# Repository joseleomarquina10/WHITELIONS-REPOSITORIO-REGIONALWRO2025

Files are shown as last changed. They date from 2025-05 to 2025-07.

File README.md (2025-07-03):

# **TABLA DE CONTENIDOS** 

- [**NUESTRO RECORRIDO**](https://github.com/joseleomarquina10/WHITELIONS-REPOSITORIO-REGIONALWRO2025/tree/main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)
- [**IDEAS Y PRINCIPIOS**](https://github.com/joseleomarquina10/WHITELIONS-REPOSITORIO-REGIONALWRO2025/tree/main/OTRO#ideas-y-principios)
- [**DOCUMENTACIÓN DEL HARDWARE**](https://github.com/joseleomarquina10/WHITELIONS-REPOSITORIO-REGIONALWRO2025/tree/main/ESQUEMAS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)
- [**DOCUMENTACIÓN DEL SOFTWARE Y DEL CÓDIGO ARDUINO**](https://github.com/joseleomarquina10/WHITELIONS-REPOSITORIO-REGIONALWRO2025/tree/main/SRC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)
- [**FOTOS DEL EQUIPO**](https://github.com/joseleomarquina10/WHITELIONS-REPOSITORIO-REGIONALWRO2025/tree/main/FOTOS-EQUIPO)
- [**FOTOS DEL VEHÍCULO**](https://github.com/joseleomarquina10/WHITELIONS-REPOSITORIO-REGIONALWRO2025/tree/main/FOTOS-VEH%C3%8DCULO)
- [**VIDEOS** ](https://github.com/joseleomarquina10/WHITELIONS-REPOSITORIO-REGIONALWRO2025/tree/main/VIDEO)

# **NUESTRO RECORRIDO**

Mediante este repositorio les mostraremos detalladamente el proceso y recorrido del proyecto WHITELIONS, con esto buscamos explicar paso por paso y ordenadamente la construcción de nuestro carro llamado WHITELION, así como también destacar su evolución y nuestro aprendizaje de cada falla, pues para nosotros fallar no es fracaso sino una oportunidad para acercarnos más al éxito.

## **EQUIPO** 

Nuestro equipo consiste de dos miembros y un coach, somos WHITELIONS de Yaracuy. Este es nuestro tercer año participando juntos en WRO, pero esta es nuestra primera edición en la categoría Fututos Ingenieros.  A continuación, se les presenta los integrantes del equipo:

    MIEMBROS:

-	Guillermo Herrera del Colegio El Ángel 
    - guillermoaherrerab@gmail.com

-	José Leonardo Marquina del Colegio Los Ángeles
    - Joseleonardomarq10@gmail.com

    COACH:

-	Luis Barrios
    - luisgbarriosm@gmail.com

Les presentamos los links a nuestras redes:

- Youtube: https://www.youtube.com/@WhiteLions-r5q
    Aquí pueden encontrar videos del desenvolvimiento del vehículo.

- Instagram: https://www.instagram.com/whitelions.wro?igsh=MWYzM2lkdWxreDZrdw==
    Aquí pueden encontrar novedades de nosotros.

## **PRIMEROS PROTOTIPOS Y EVOLUCIÓN DEL DISEÑO**

- ### **Primer Prototipo**
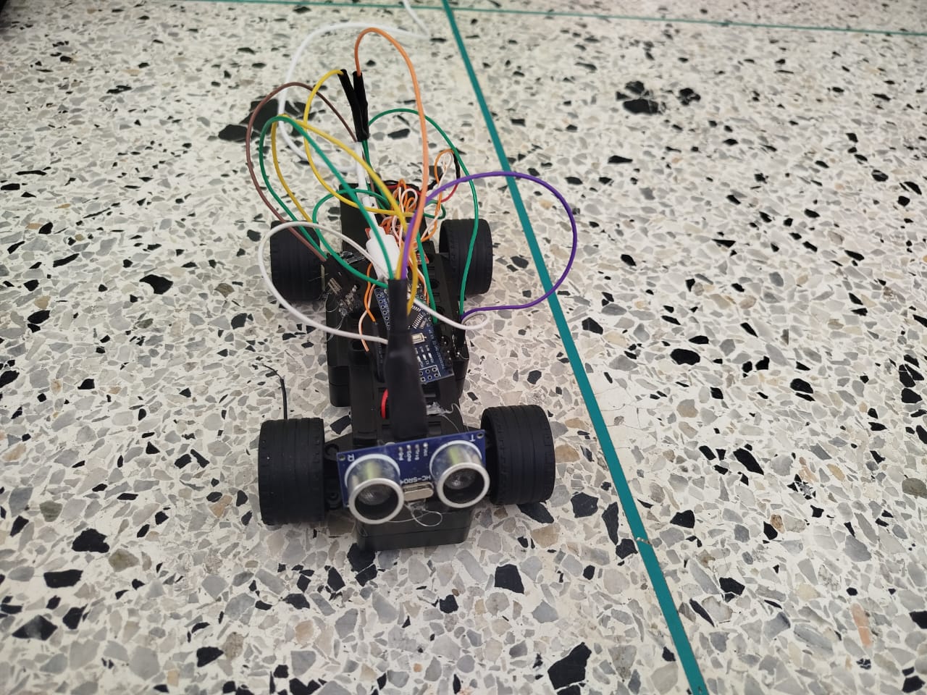
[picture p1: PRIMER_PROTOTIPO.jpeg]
PRIMER PROTOTIPO


Originalmente, utlizamos un kit de carro de lego al cual le instalamos una tarjeta arduino nano y un sensor de ultrasonido, aprovechamos el sistema de dirección y tracción que contaba el carro. Por una parte la tracción funcionaba con un motor dc y por la otra parte la dirección también contaba con un motor dc pero controlaba su radio de giro con una pieza de abanico que limitaba el giro. Además el carro tenía un driver de motor para controlar estos.

Todo este mecanismo lo conectamos con la tarjeta Arduino y aquí nació el primer prototipo del WHITELION, el cual únicamente giraba a la izquierda al detectar una pared al frente y gracias al mecanismo de engranajes de la tracción iba a alta velocidad.

Este primer prototipo nos sirvió para realizar una gran cantidad de pruebas así como también para darnos cuenta de muchas cosas que debíamos mejorar. Rápidamente nos dimos cuenta de que la dirección presentaba muchos fallos pues era controlada por un motor dc, además el chasis del carro era demasido pequeño y estrecho, lo que iba a dificultar ubicar el resto de componentes necesarios. 

- ### **Primer Modelo en Tinkercad**
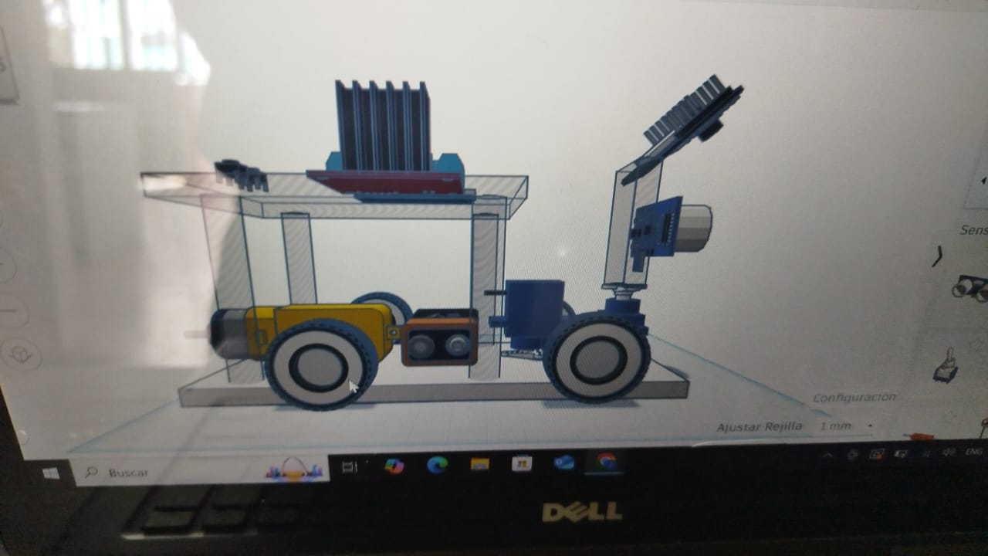
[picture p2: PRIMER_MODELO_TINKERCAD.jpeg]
PRIMER_MODELO_TINTERCAD


Por lo anterior, realizamos un rediseño para imprimir en 3D todo el chasis y la dirección, sin embargo nos quedamos con las ruedas delanteras y su mecanismo de giro, además la nueva dirección sería controlada por un servomotor para más precisión al girar.

Nuestro principio es que el carro sea pequeño por eso definimos el nuevo chasis de dimensiones de 10x15 cm, pero igualmente nos dimos cuenta del poco espacio, por ello decidimos hacerle un segundo chasis al carro y de esta forma habrían dos: Chasis superior, con los controladores y la batería; y chasis inferior, con la traccion, dirección y el sensorores. 

Del carro anterior, también definimos que el ultrasonido funcione como un radar y que se mueva constantemente por un servomotor para detectar su entorno y de alli decidir a donde girar, por ello pensamos en utilizar una torre arriba del servo para colocar el ultrasonido y una posible cámara, además utilizamos un solo motor dc para la tracción para no complicar la programación y porque al probar con dos constantemente se soltaban del eje.

Incorporamos el driver de motor dc L298N para poder controlar la velocidad a través del pwm y por sus conexiones atornilladas, para asegurar una conexión firme. por la misma razón incluimos una base expansora de arduino nano para atornillar.

- ### **Primer Carro Funcional**
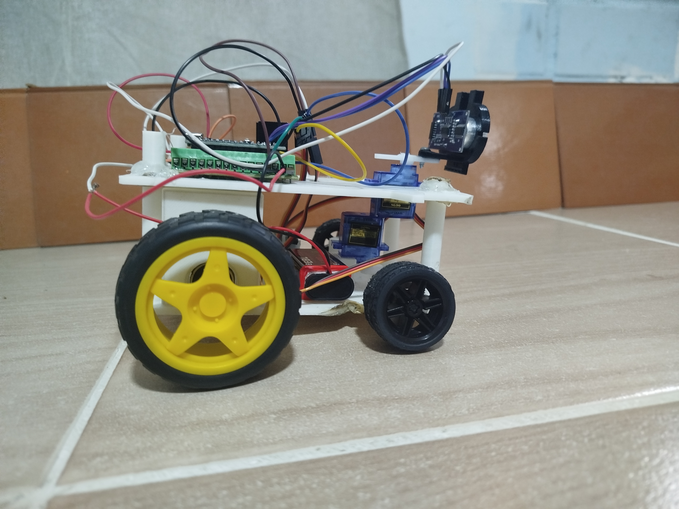
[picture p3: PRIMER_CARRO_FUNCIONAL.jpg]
PRIMER_CARRO_FUNCIONAL


Tras este rediseño notamos que aún era necesario más espacio por ello expandimos el chasis superior a las mismas dimensiones del inferior. 

Notamos que existía un espacio aprovechable en el chasis infeior por el uso de un solo motor así que allí ubicamos la batería y para que todos los cables pasaran de buena forma de chasis a chasis, hicimos una abertura en el superior.

Tras esta expasión del chasis superior ya no podíamos instalar el radar en el chasis inferior, por lo que decidimos hacerlo arriba y con impresión 3D llegamos a este nuevo prototipo, el cual usaríamos en nuestra primera regional.

### **DISEÑO ACTUAL**
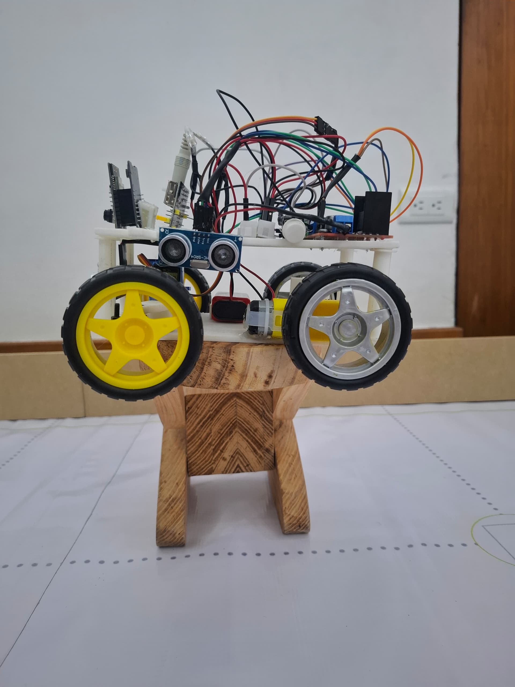
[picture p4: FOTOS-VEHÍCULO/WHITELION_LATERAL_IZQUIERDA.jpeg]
DISEÑO_ACTUAL


Tras nuestra primera regional decidimos descartar el radar pues presentaba muchos fallos, en su lugar agregamos tres sensores de ultrasonido (Uno apuntando hacia el frente y los otros hacia los laterales, uno a la derecha y otro a la izquierda) de tal forma de que el carro detecte cuando haya un vacío y girar hacia allá. Además cambiamos las ruedas de lego por otras de motor DC e incorporamos la cámara ESP32 CAM para la vuelta de obstáculos, sin embargo notamos rápidamente que coincide en posición con el ultrasonido central, por ello dejamos el ultrasonido en el chasis inferior y la cámara en el superior.

También incorporamos una fuente de alimentación para distribuir el voltaje entre la arduino, el driver y la cámara; adicional a esto añadimos dos líneas negativas y positivas de protoboard para complementar.

Debido a los nuevos componentes agregados tuvimos que expandir ambos chasis a dimensiones de 17,5x15 cm, además de reforzar el grosor de la barra de dirección para hacerla más resistente.

Y así llegamos a nuestro diseño actual.

# **CONCLUSIÓN**

Este proyecto fue realmente difícil de desarrollar, pero nos dió mucho aprendizaje dentro del mundo de la robotica y nos brindó experiencias innolvidables, enseñandonos a como manejar los problemas de la mejor manera posible, ya sea en programación del proyecto o en el armado cuando nada queria funcionar y cuando nada se ajustaba a lo que buscabamos hacer, y que aún asi poder salir adelante y hacer un proyecto funcional de competencia, motivandonos a seguir participando en estas competencias.

# **AGRADECIMIENTOS**

Primeramente nos sentimos agradecidos con Dios, con nuestro tutor Luis Barrios y con nuestros padres, por apoyarnos siempre y formar parte de todo este recorrido en futuros ingenieros. Agradecemos de la misma forma a nuestra casa de las olimpiadas MATICES, por darnos sus espacios para poder armar y desarrollar el carro, a nuestros profesores Johan Goyo y Rafael Linarez por orientarnos y a nuestros colegios "El Ángel" y "Los Ángeles".

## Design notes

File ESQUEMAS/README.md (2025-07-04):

# **ESQUEMAS**

## **DOCUMENTACIÓN DEL HARDWARE**

### **LISTA DE COMPONENTES**
 
Instalamos una gran cantidad de sensores y componentes al vehículo. A continuación les presentamos una lista con cada uno de estos:

- Tarjeta Arduino Nano Ch340              x1
- Base Expansora para Arduino Nano        x1
- ESP32 cam Arduino                       x1
- Motor DC Caja Reductora 200 rpm         x1
- Ruedas de Motor DC (Tracción)           x2
- Ruedas de Motor DC (Dirección)          x2
- Micro ServoMotor Sg90 90g               x1
- Sensor Ultrasonido Hc-sr04              x3
- Driver de Motor DC L298N                x1
- Batería 9v y 5400 mAh                   x1
- Rolinera                                x1
- Barra Metálica (tracción)               x1
- cilindro hueco de plástico              x1
- Fuente de Alimentación Mb102            x1
- Pulsador                                X1
- Interruptor                             x1
- Línea positiva y negativa de protoboard x2 

### **ENSAMBLADO**

El carro se divide en dos bases: La base inferior y la base superior. Cada base lleva por dimensiones 17,5x14cm (se incluyen las alas para las ruedas de dirección).

En la siguente tabla se explica en que base se encuentra cada componente Y cada Material:

| BASE INFERIOR | BASE SUPERIOR |
|---|---|
|Chasis Inferior |Chasis Superior |
|Motor DC |Arduino Nano |
|Micro ServoMotor  |Base expansora para arduino nano |
|Rolinera |Driver de motor L298N | 
|Barra Metálica |2 línea positiva y negativa de protoboard |
|Cilindro Hueco |Botón de encendido |
|4 Ruedas motor DC |Fuente de alimentación (con interruptor incluido) |
|Batería 9v |2 sensores ultrasonido |
|Soporte Tracción  |Cámara ESP32 CAM |
|Soporte Dirección | |
|Barra Dirección | | 
|4 Soporte Cilindro| | 
|Sensor ultrasonido| | 
|Soporte Servo | |
|2 Soporte Batería | |  

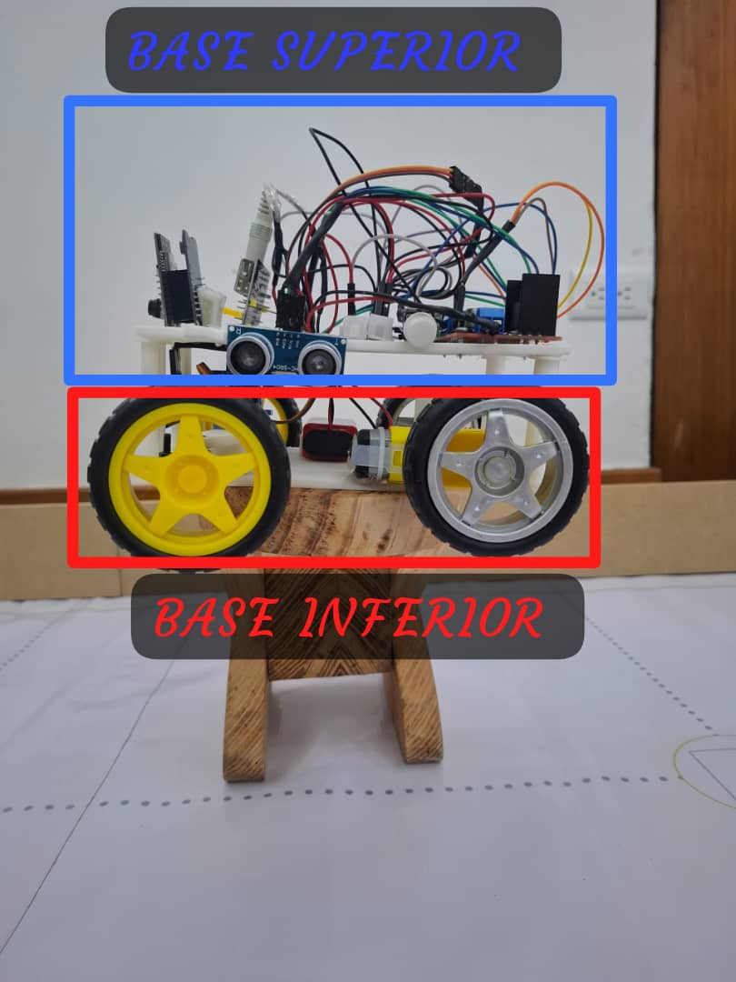
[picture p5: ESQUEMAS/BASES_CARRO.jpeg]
BASES_CARRO


### **BASE INFERIOR**

Esta es la base de tracción, dirección y donde se ubica la batería, además del ultrasonido central.

 Para la dirección Diseñamos un soporte en forma de bloque para ubicar el servo boca abajo, una barra para unir las dos ruedas delanteras y dos soportes en forma de triángulo (similar a las alas para colocar las ruedas) para sostenerlas y mantenerlas en un eje vertical. De esta forma ubicamos las ruedas a una distancia entre sus ejes verticales de 12 cm (Cada eje vertical dista 1cm del chasis de tal forma que las ruedas tengan el mayor radio de giro). Los ejes verticales de las ruedas y del servo deben estar alineados para moverse en paralelo. Ubicamos estos ejes a una distancia de 3,25 cm del borde frontal del chasis, y así dejar espacio para la barra de dirección, esta mide 13 cm (cubre la distancia entre eje a eje de cada rueda y un poco más). El eje del servo se encuentra a 6 cm de cada eje vertical de las ruedas delanteras. La distancia total de punta a punta de las ruedas de dirección es 19,5 cm.

 Para la tracción ubicamos el motor DC tal que su eje horizontal se encuentre a 3cm del borde posterior del chasis, una rueda la unimos directamente al motor mientras que la otra la conectamos por un eje compuesto por una barra metálica y esta se conecta al motor DC siendo envuelta por un cilindro hueco de lapicero y una pieza de lego negra, la barra se fija al cilindro con silicón para que no quede inestable al girar, además la barra también se fija a una rolinera de diámetro 2cm para asegurar que ambas ruedas estén a una misma altura. Luego se fija el soporte en forma de U en la rolinera para dejarla fija. Las ruedas traseras se encuentran a una distancia, cada una, de 1,5 cm del chasis y la distancia total de punta a punta de ambas ruedas de tracción es 18 cm.

 Note que en la parte central del chasis inferior aún queda un gran espacio aprovechale, allí ubicamos dos soportes con forma de pared para fijar la batería, estos soportes distan 1,5 cm del borde derecho del chassis y tienen una distancia entre sí de 2,8cm (el ancho de la batería). La batería se ubica con sus conectores apuntando hacía la izquierda y su puerto USB apuntando hacia la derecha, de manera que sea práctico cargarla sin desmontarla el carro.

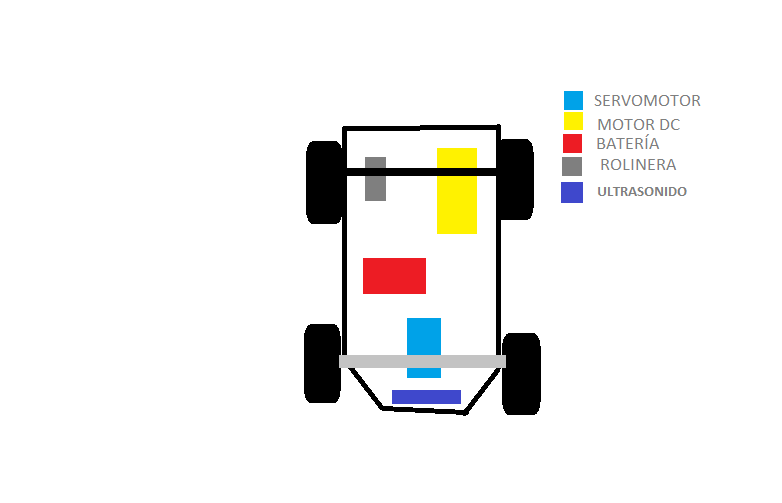
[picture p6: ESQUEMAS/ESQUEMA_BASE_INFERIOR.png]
ESQUEMA_BASE_INFERIOR


### **BASE SUPERIOR**

Esta es la base de control, con las tarjetas controladoras y la mayaroría de sensores ultrasonidos junto a la cámara, además de la fuente de alimentación.

Instalamos la Arduino Nano y el driver L298N en la parte posterior de esta base, pusimos la Arduino en una base expansora para atornillar las conexiones de cables y para poder atornillar la tarjeta al chasis así como también el driver, de esta forma evitamos que se muevan y que se puedan desconectar los cables. Las líneas positiva y negativa de protoboard las fijamos con pega 2cm más adelante de las tarjetas para dejar espacio para la conexión de cables (pues las conexiones a las tarjetas se hacen horizontales). Diseñamos una abertura para esta base y así pasar los cables del chasis inferior al superior. Ahora bien, 2cm después de la abertura se instala verticalmente la fuente de alimentación. 

Los sensores ultrasonidos laterales se instalan justo detrás de las alas del chasis superior, deben estar apuntando ligeramnete hacia abajo para evitar detectar cosas externas a la pista. Similarmente la cámara se instala en la parte frontal de esta base, apuntando ligeramente hacia abajo.

Con respecto a las líneas de protoboard y la fuente de aliemntación, una línea corresponde al voltaje de 5v, es decir esta línea viene alimentada por los 5v de la fuente de alimentación y aquí se conectan la Arduino Nano, los sensores ultrasonidos y el servo de la dirección. Mientras que la segunda línea está alimentada directamente por la batería y aquí se conecta el driver L298N, pues requiere de los 9v. Por otro lado la ESP32 CAM se alimenta directamente por los 3.3v de la fuente de alimentación.

En general las conexiones se realizaron con cables dupont Macho-Macho, Hembra-Hembra y Macho-Hembra, evitamos usar cables sin cabeza pues pueden soltarse y complicar la conexiones.

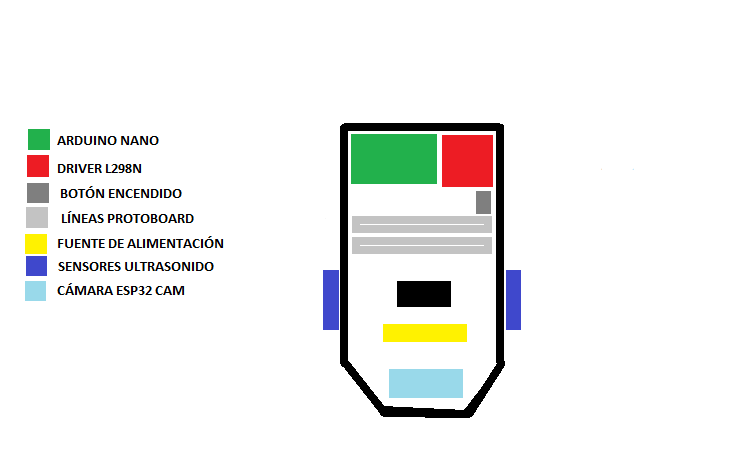
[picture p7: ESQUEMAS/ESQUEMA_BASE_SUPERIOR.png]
ESQUEMA_BASE_SUPERIOR


### **CIRCUITO ELÉCTRICO**

A continuación se les presenta el circuito eléctrico de la tarjeta Arduino con los demás componentes (en este esquema no se incluye la ESP32 CAM)

CIRCUITO_ELECTRICO

Ahora bien, para la ESP32-CAM, TX y RX de la cámara se conecta con el TX y RX de la Arduino Nano respectivamente, el GND se conecta a la línea negativa GND de la protoborad. Esta se alimenta al conectarse directamente a los 3,3V de la fuente de alimentación.

Para más detalles sobre la definición de pines pueden ver [DEFINICIÓN DE PINES](https://github.com/joseleomarquina10/WHITELIONS-REPOSITORIO-REGIONALWRO2025/tree/main/SRC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)

## **DESEMPEÑO DEL CARRO**

A continuación se tienen los esquemas del desempeño del carro en las vueltas:

### VUELTA LIBRE

- El carro siempre se mueve adelante. Se detiene cuando haya realizado 12 giros exactos.

- Al detectar un vacío lateral de más de 200 cm y que la distancia frontal es de 60 cm, gira hacia este lado de tal forma de mantenerse en paralelo a la pared, hasta quedar en 90 grados con respecto a su trayectoria inicial.

ESQUEMA_GIRO_VUELTA_LIBRE

- Sí se encuentra a una distancia de menos de 20 cm de la pared (o queda apuntando a la pared) gira levemente para despegarse de ella y nivelarse.

ESQUEMA_NIVELACIÓN_VUELTA_LIBRE

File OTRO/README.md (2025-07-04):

# **IDEAS Y PRINCIPIOS**

##  **CONSTRUCCIÓN Y MECANISMO DEL CARRO**

- Decidimos que el carro fuera pequeño para que pudiera maniobrar más fácilmente y tuviera mejor tiempo de reacción. De allí fijamos las dimensiones para el chasis de 15x13 cm y lo imprimimos en 3D.

- Con estas dimensiones, claramente no podíamos instalar todos los componentes necesarios en la base; por tanto, implementamos un segundo piso para el carro. Así dejamos dos chasis: el inferior de mecanismo, con la tracción, la dirección y la batería; y el superior de control, con la tarjeta Arduino Nano, el driver de motor y los sensores.

- Para la dirección consideramos usar un servomotor para controlar el giro de las ruedas delanteras mediante una barra que conecte ambas ruedas con el servo. Tomamos en cuenta que fuera una barra metálica, pero al notar que dificultaba mucho el proceso de armado y desarmado, además de provocar fallas en las conexiones, decidimos imprimir esta barra en 3D. Reutilizamos unas ruedas de un kit de LEGO y replicamos los soportes de estas en 3D junto a la barra.

- Para la tracción, decidimos no usar dos motores DC, pues se soltaban constantemente. De allí decidimos dejar solo un motor DC para simplificar la programación y el mecanismo. Usamos ruedas de motor DC amarillo, una conectada directamente al motor y otra unida por una barra metálica a un lapicero que funcionó como eje. Para centrar esta rueda, utilizamos una rolinera para dejar fijo el eje y evitar rebotes.

- Como aún había espacio en el chasis inferior debido al uso de solo un motor, decidimos colocar la batería en ese espacio.

- Notamos que habría dificultades para conectar los cables de batería, motor y servo a los controladores del chasis superior. Por ello dejamos una abertura en el chasis superior para los cables.

- La ubicación del Arduino y el driver la dejamos en la parte trasera del chasis superior, mientras que los sensores los dejamos en la parte frontal; además, el pulsador y el interruptor los ubicamos a los costados.

- Decidimos utilizar el driver L298N por su capacidad para PWM y porque las conexiones se atornillan, garantizando buena conexión de los cables y que no se suelten. Por la misma razón, utilizamos una base expansora de atornillado para el Arduino.

- Originalmente pensamos en utilizar un radar en la parte frontal del chasis superior, constituido por un servomotor y un sensor de ultrasonido, para que el carro detectara y diferenciara la pared del vacío. Sin embargo, esto no resultó y complicó el proyecto.

- Tras nuestra primera regional, descartamos la idea anterior e implementamos al carro tres sensores de ultrasonido fijos (uno apuntando a la derecha, otro hacia el centro y el otro a la izquierda), además de una cámara ESP32-CAM para detectar los colores en la vuelta de obstáculos.

- Rápidamente notamos que el ultrasonido central y la cámara coincidían en ubicación; por ello, dejamos el ultrasonido en la parte delantera del chasis inferior y la cámara en la parte superior.

- Además, decidimos alargar los chasis a nuevas dimensiones de 17,5x15 cm para poder implementar una fuente de alimentación y distribuir el voltaje: 5V para el Arduino y 3,3V para la ESP32-CAM.

- Cambiamos las ruedas de la dirección por ruedas de motor Dc para mejor estabalidad al girar.

- También notamos en esa primera regional que los sensores de ultrasonido deben apuntar hacia abajo, pues si están en la parte superior pueden detectar objetos externos a la pista. Utilizamos el mismo razonamiento para ubicar la cámara apuntando hacia abajo.

##  **PARA LA VUELTA LIBRE**

- Originalmente pensamos que el carro se detuviera al detectar la primera pared y, con el radar, definir hacia qué dirección tenía que girar. Esto lo realizaría una sola vez y después, con el sentido definido, giraría automáticamente en esa dirección al detectar una pared a unos 50 cm de distancia. Sin embargo, esta idea no funcionó bien, pues la programación se complicó y el servo, junto con el ultrasonido, fallaban constantemente.

- Tras la primera regional, decidimos dejar atrás la idea del radar e implementar los tres sensores de ultrasonido y la cámara ESP32-CAM tal y como fue explicado anteriormente. Con esto, desarrollamos un nuevo plan para la vuelta libre como se detalla a continuación.

- El carro debe guardar las tres distancias que detectan los sensores de ultrasonido al encenderse, de tal forma que pueda definir en qué recuadro de los seis posibles se encuentra el punto de salida.

- Cuando el carro avance y uno de los ultrasonidos laterales detecte una distancia mayor a un metro, es porque debe haber un vacío y, por tanto, debe girar hacia ese vacío.

- Si el carro no queda en paralelo a las paredes o queda apuntando hacia una pared después del giro, entonces debe acomodarse. Por tanto, si la distancia de un ultrasonido lateral a la pared es menor a 15 cm, debe girar un poco al lado contrario para despegarse de la pared.

- Después de dar las tres vueltas, el carro —a una velocidad lenta— debe buscar llegar a las medidas iniciales para estacionarse en el punto de inicio.

- En general, el carro debe ir a una velocidad controlada para dar suficiente tiempo a los sensores de detectar el entorno.

## **PARA LA VUELTA DE OBSTÁCULOS**

- Dividimos los cuadros grandes de la pista en tres carriles: derecho, central e izquierdo. Con esto definimos tres funciones para el carro: ir al carril derecho, al central y al izquierdo. De esta forma, si detecta un obstáculo rojo irá al carril derecho y, tras pasarlo, se devolverá al carril central; análogamente, hará lo mismo pero hacia la izquierda si detecta un obstáculo verde.

- La función de volver al carril central después de evadir un obstáculo es necesaria, pues en un cuadro grande puede haber varios y lo ideal es que el carro se mantenga en el centro para evadirlos y girar más fácilmente. Además, el carro puede encontrarse con el aparcadero y provocar una falla de lógica, por ello debe mantenerse siempre en el carril central.

- Al llegar a un cuadro grande de esquina (es decir, una pared), el carro debe girar hacia atrás en sentido contrario al vacío y quedar centrado apuntando hacia él. Esto asegura que cuando llegue a una nueva pared vuelva a quedar centrado.

- Después de dar las tres vueltas, el carro debe dar otra vuelta adicional y mantenerse pegado a la pared, de tal forma que no se desalineé. Cuando detecte el aparcadero debe ejecutar una función de aparcado, que consiste en evadirlo, quedarse quieto con el aparcadero al lado, girar hacia atrás en sentido opuesto a donde se encuentra el aparcadero (de tal forma que quede viendo hacia él de frente, similar a como se explica cuando el carro llega a un cruce), y finalmente moverse hacia adelante hasta entrar en el aparcadero.

- En general, el carro debe ir a una velocidad muy controlada para dar suficiente tiempo a la cámara de detectar el entorno.

- No se utilizan mucho los sensores de ultrasonido en la vuelta de obstáculos, pues pueden confundirse fácilmente con los mismos obstáculos. Se prioriza el uso de la cámara.

Para más detalles del desempeño del carro en la ronda libre y de obstáculos pueden ver [DESEMPEÑO DEL CARRO](https://github.com/joseleomarquina10/WHITELIONS-REPOSITORIO-REGIONALWRO2025/tree/main/ESQUEMAS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)

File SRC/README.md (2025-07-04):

# **DOCUMENTACIÓN DEL SOFTWARE Y DEL CÓDIGO ARDUINO**

## **DEFINICIÓN DE PINES**

En las siguentes tablas se ve asignado cada pin con su funcionamiento:

- TARJETA ARDUINO NANO

| CONCEPTO DEL PIN | PIN ASIGNADO |
|---|---|
| TRIGGER_DERECHA | d2 |
| ECHO_DERECHA | d3 |
| TRIGGER_CENTRAL | d4 |
| ECHO_CENTRAL | d5 |
| TRIGGER_IZQUIERDA  | d6 |
| ECHO_IZQUIERDA | d7 |
| SERVO | d8 |
| MOTOR_IN3 | d9 |
| MOTOR_IN4 | d10 |
| ENB | d11 |
| ENCENDIDO | d12 |
| ALIMENTACIÓN 5V | VCC |
| NEGATIVO | GND |
| TRANSMISIÓN | TX |
| RECEPCIÓN | RX |

- DRIVER L298N 

| CONCEPTO DEL PIN | PIN ASIGNADO |
|---|---|
| MOTOR_IN3 | IN3 |
| MOTOR_IN4 | IN4 |
| ENB | ENB |
| CONEXIÓN_OUT3 | OUT3 |
| CONEXIÓN_OUT4 | OUT4 |
| ALIMENTACIÓN 5V | +5V |
| ALIMENTACIÓN BATERíA| +12V |
| NEGATIVO | GND |

- CÁMARA ESP32-CAM

| CONCEPTO DEL PIN | PIN ASIGNADO |
|---|---|
| TRANSMISIÓN | TX |
| RECEPCIÓN | RX |
| ALIMENTACIÓN | 3.3V |
| NEGATIVO | GND |

- FUENTE DE ALIMENTACIÓN

| CONCEPTO DEL PIN | PIN ASIGNADO |
|---|---|
| ALIMENTACIÓN 5V | 5V |
| NEGATIVO 5V | GND 5V |
| ALIMENTACIÓN 3.3V | 3.3V |
| NEGATIVO 3.3V | GND 3.3V |

## **ESTRUCTURA Y LÓGICA DEL CÓDIGO**

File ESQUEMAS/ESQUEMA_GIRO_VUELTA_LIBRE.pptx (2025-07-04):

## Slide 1

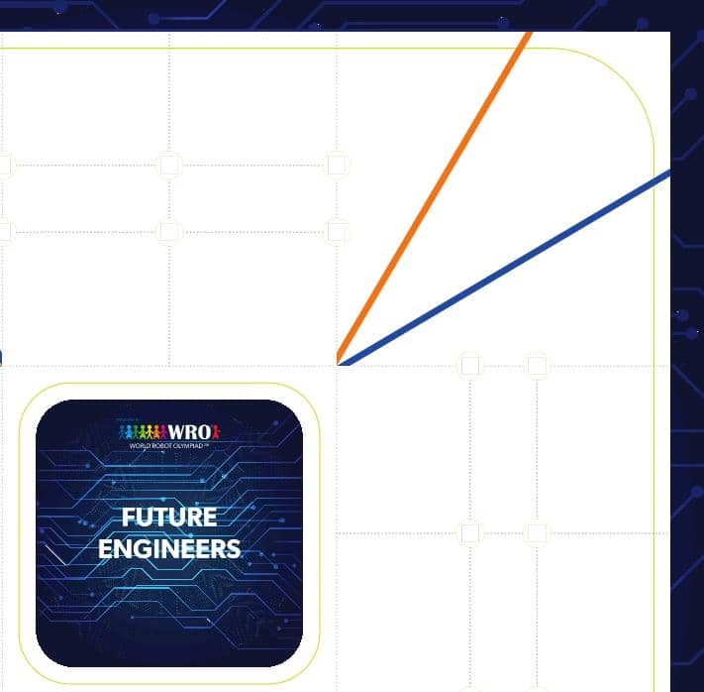
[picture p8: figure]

GIRO EN PARALELO A LAS PAREDES

DISTANCIA MENOR A 60 CM

DISTANCIA MAYOR A 200CM

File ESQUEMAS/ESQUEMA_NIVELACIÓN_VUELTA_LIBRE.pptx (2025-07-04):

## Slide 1


GIRA 13 GRADOS

DISTANCIA MENOR A 20 CM

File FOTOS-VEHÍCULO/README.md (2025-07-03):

# **FOTOS DEL VEHÍCULO**

Les presentamos a continuación una foto desde cada dirección del vehículo, además de tres fotos extra: dos de la base inferior y una de la base superior.

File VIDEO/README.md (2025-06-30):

# **VIDEOS**

En esta carpeta les mostramos un video de la vuelta libre y uno de la vuelta de obstáculos.

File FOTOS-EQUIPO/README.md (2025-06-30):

# **FOTOS DEL EQUIPO**

Les presentamos una foto del equipo y el coach, una foto de nuestro logo y una foto graciosa.

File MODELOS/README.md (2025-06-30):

# **MODELOS**

Esta carpeta contiene los modelos 3D que utilizamos durante el desarrollo del proyecto.

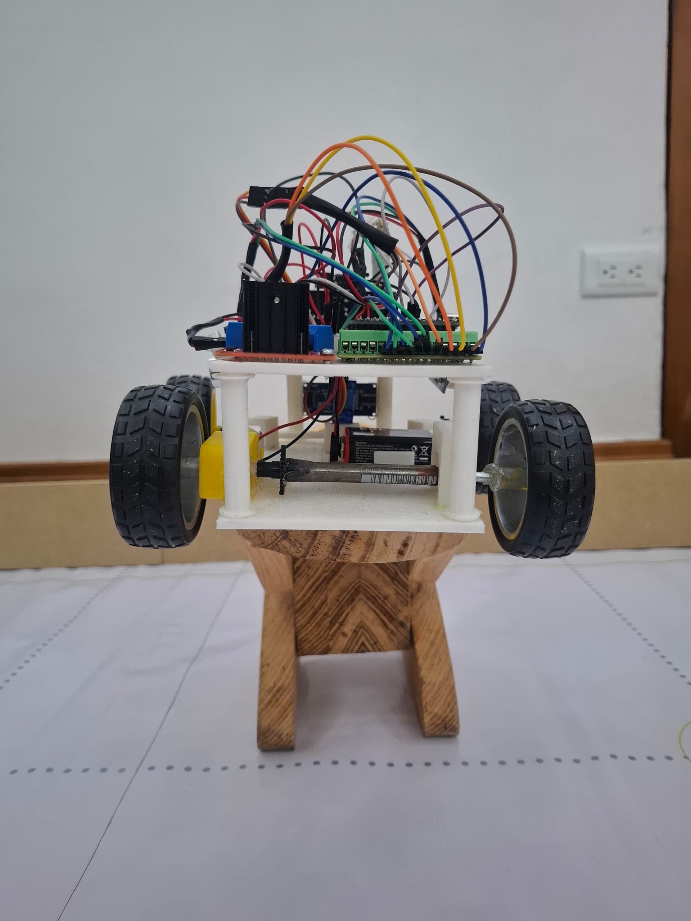
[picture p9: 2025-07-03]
FOTOS-VEHÍCULO/WHITELION_VISTA_POSTERIOR.jpeg

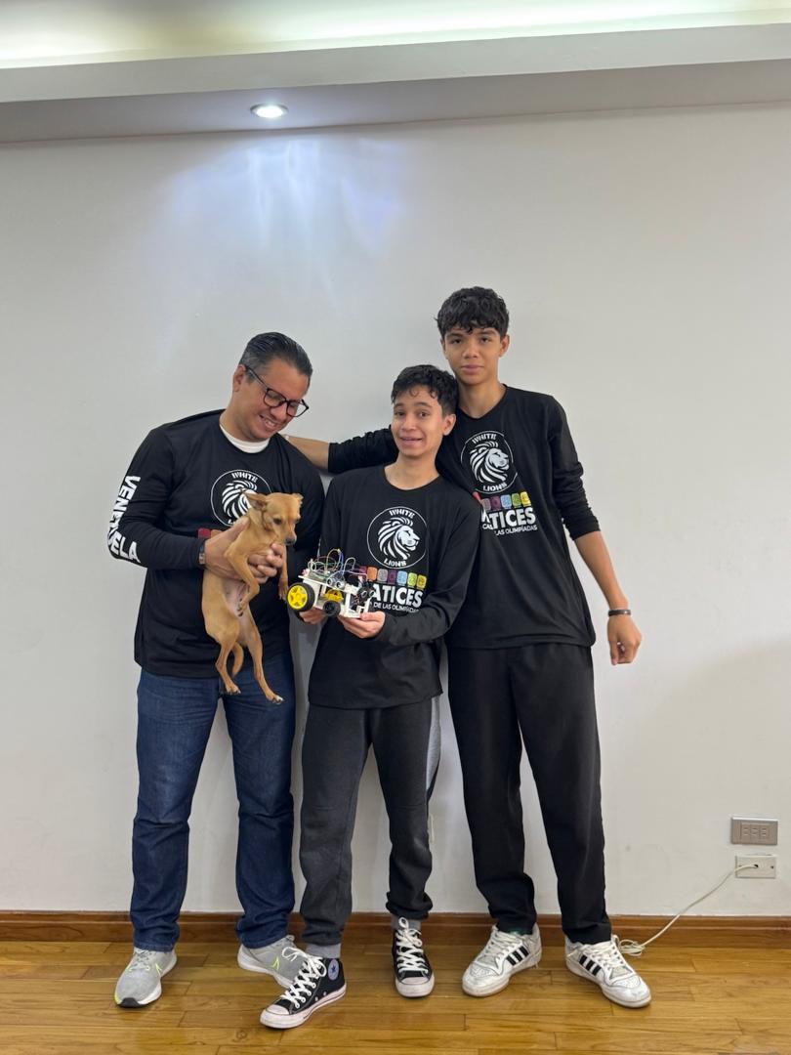
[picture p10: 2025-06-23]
FOTOS-EQUIPO/FOTO GRACIOSA.jpeg

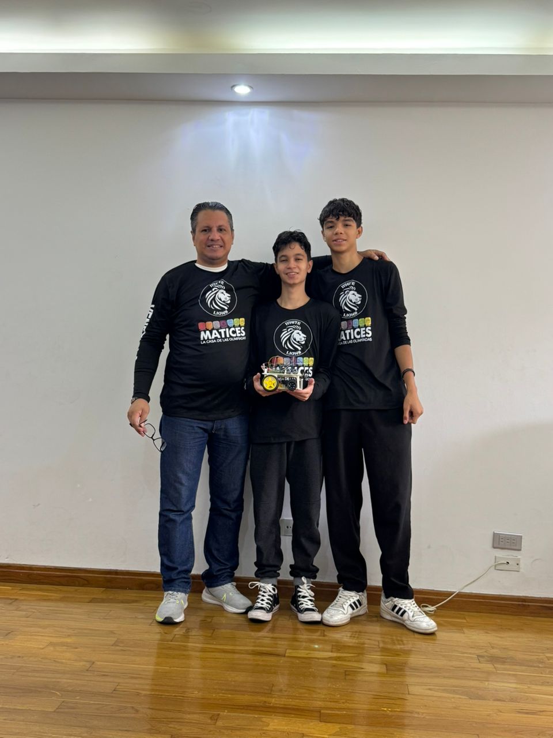
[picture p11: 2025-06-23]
FOTOS-EQUIPO/FOTO EQUIPO.jpeg

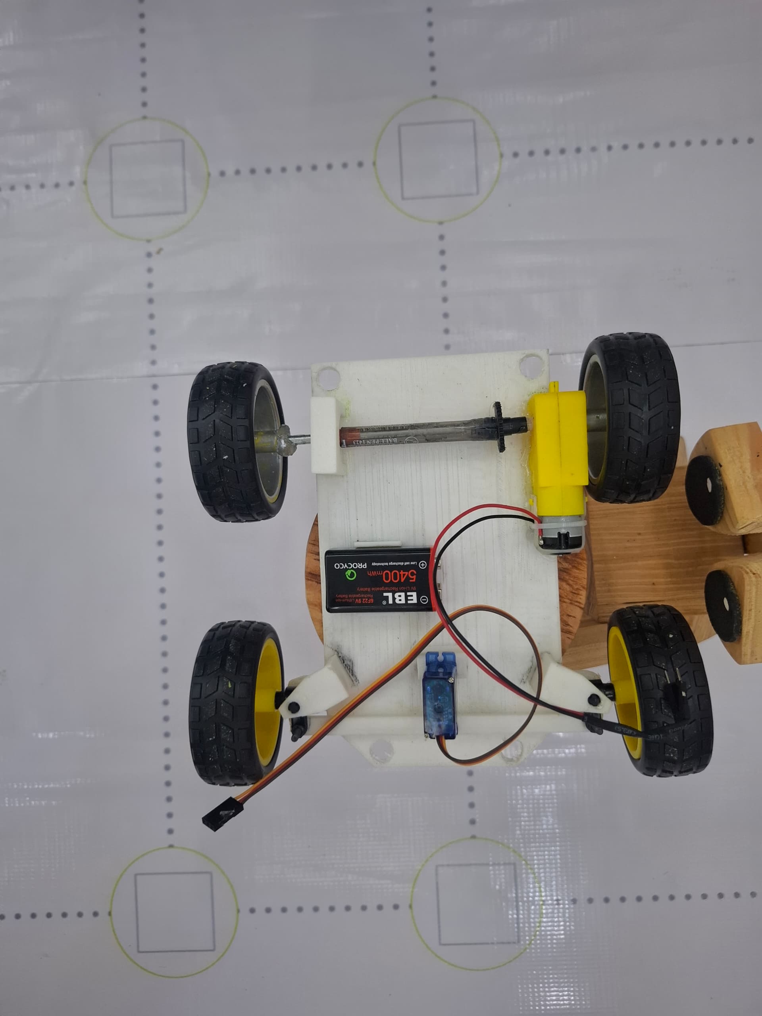
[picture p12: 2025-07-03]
FOTOS-VEHÍCULO/WHITELION_BASE_INFERIOR.jpeg

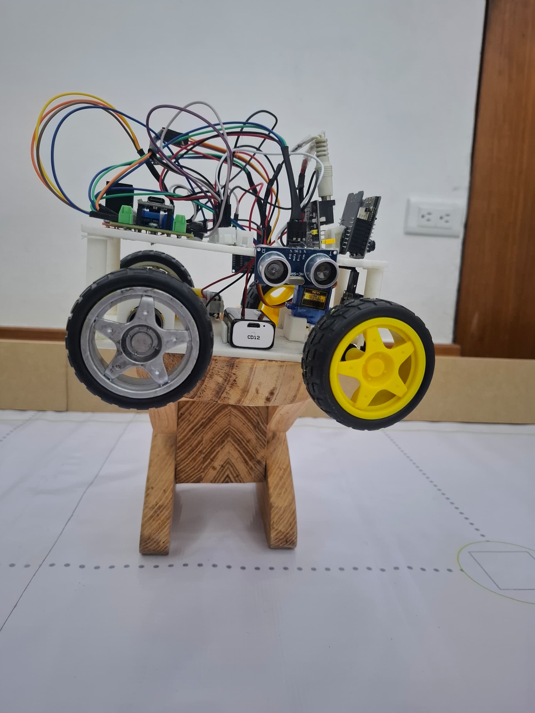
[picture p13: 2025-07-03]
FOTOS-VEHÍCULO/WHITELION_LATERAL_DERECHA.jpeg

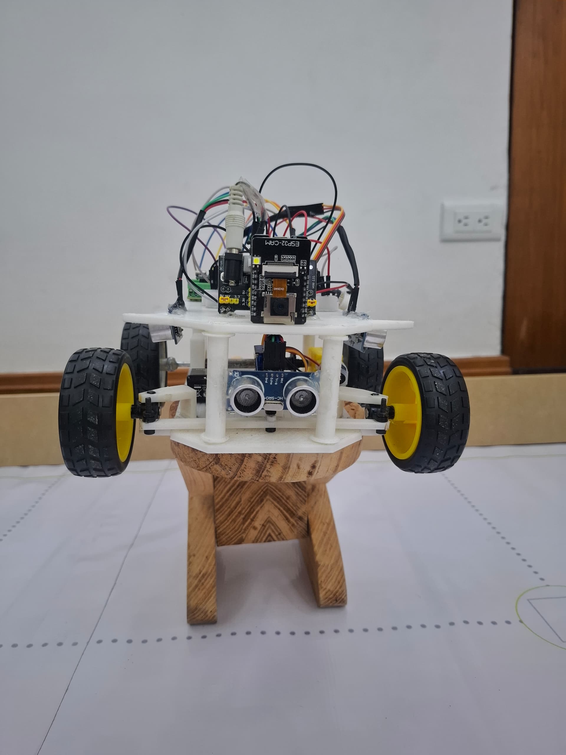
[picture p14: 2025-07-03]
FOTOS-VEHÍCULO/WHITELIONS_VISTA_FRONTAL.jpeg

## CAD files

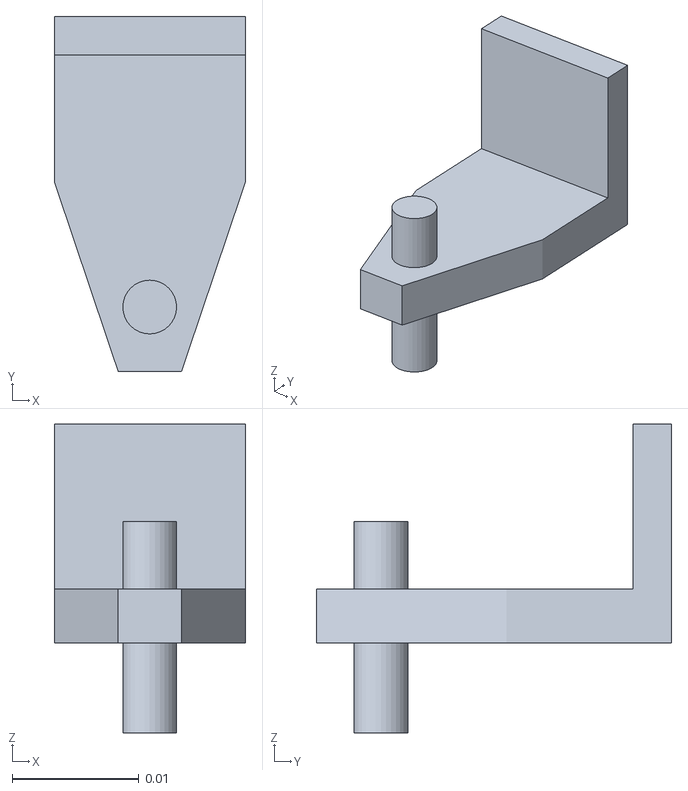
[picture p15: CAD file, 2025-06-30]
MODELOS/SOPORTE RUEDAS DIRECCION.stl
0.0151 x 0.028 x 0.0244

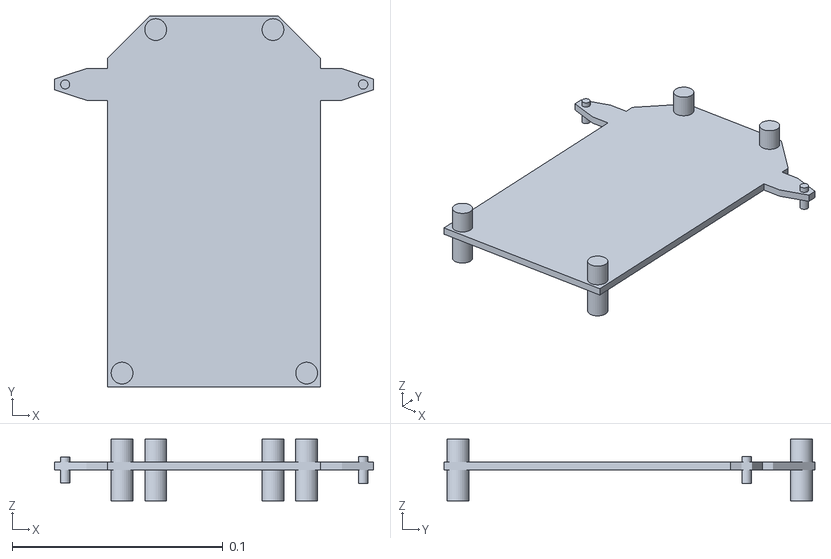
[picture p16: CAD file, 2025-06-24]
MODELOS/BASE INFERIOR.stl
0.152 x 0.176 x 0.0293

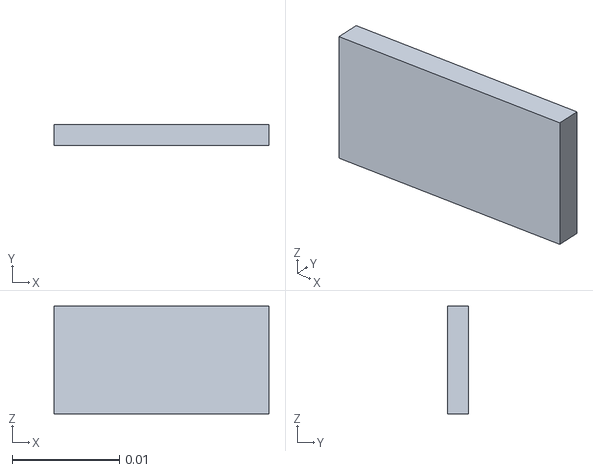
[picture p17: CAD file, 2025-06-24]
MODELOS/SOPORTE PARED.stl
0.02 x 0.002 x 0.01

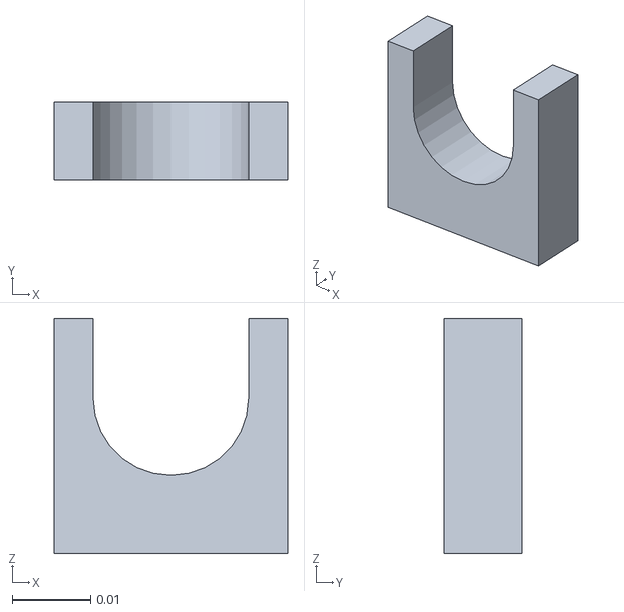
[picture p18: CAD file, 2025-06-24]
MODELOS/SOPORTE RUEDAS TRACCION.stl
0.03 x 0.01 x 0.0302

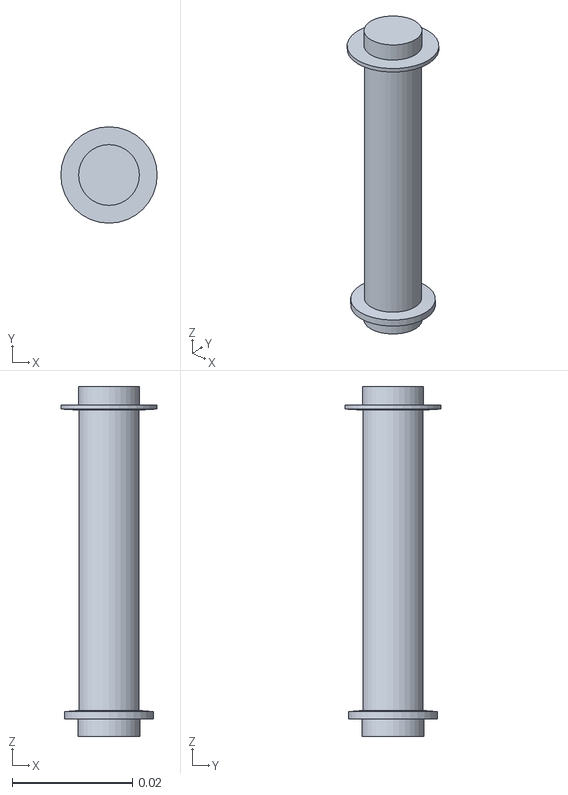
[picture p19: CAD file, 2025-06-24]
MODELOS/SOPORTE CILINDRO.stl
0.016 x 0.016 x 0.0582

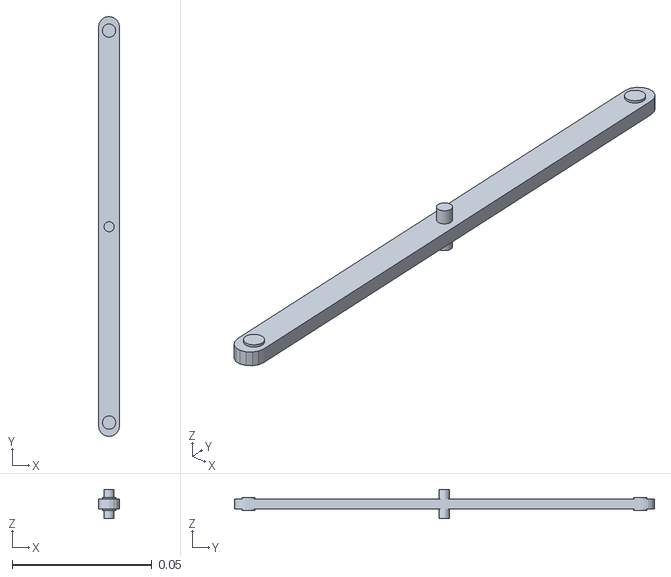
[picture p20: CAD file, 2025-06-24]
MODELOS/BARRA DIRECCION.stl
0.00755 x 0.15 x 0.0104

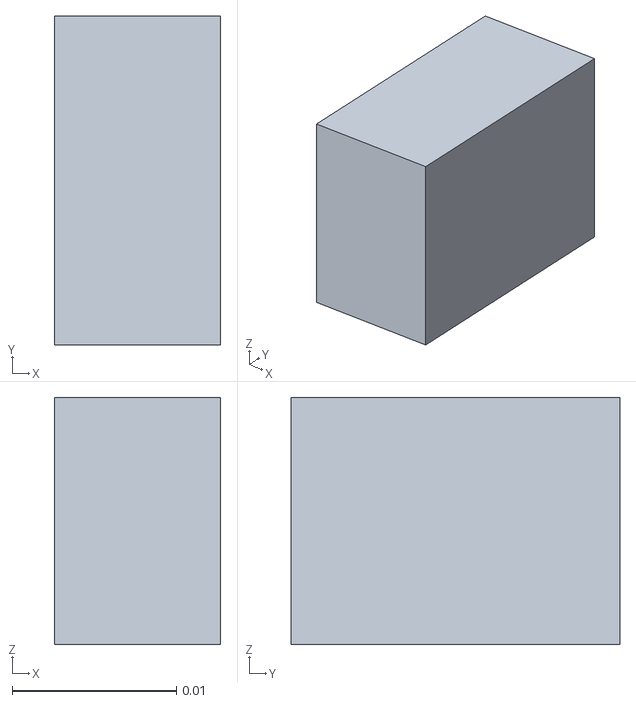
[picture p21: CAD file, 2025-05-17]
MODELOS/SOPORTE SERVOMOTOR.stl
0.0101 x 0.02 x 0.015

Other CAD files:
MODELOS/BASE SUPERIOR.stl

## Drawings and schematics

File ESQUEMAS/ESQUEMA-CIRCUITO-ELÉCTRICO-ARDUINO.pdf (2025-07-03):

A

1 | 2 | 3 | 4 | 5 | 6

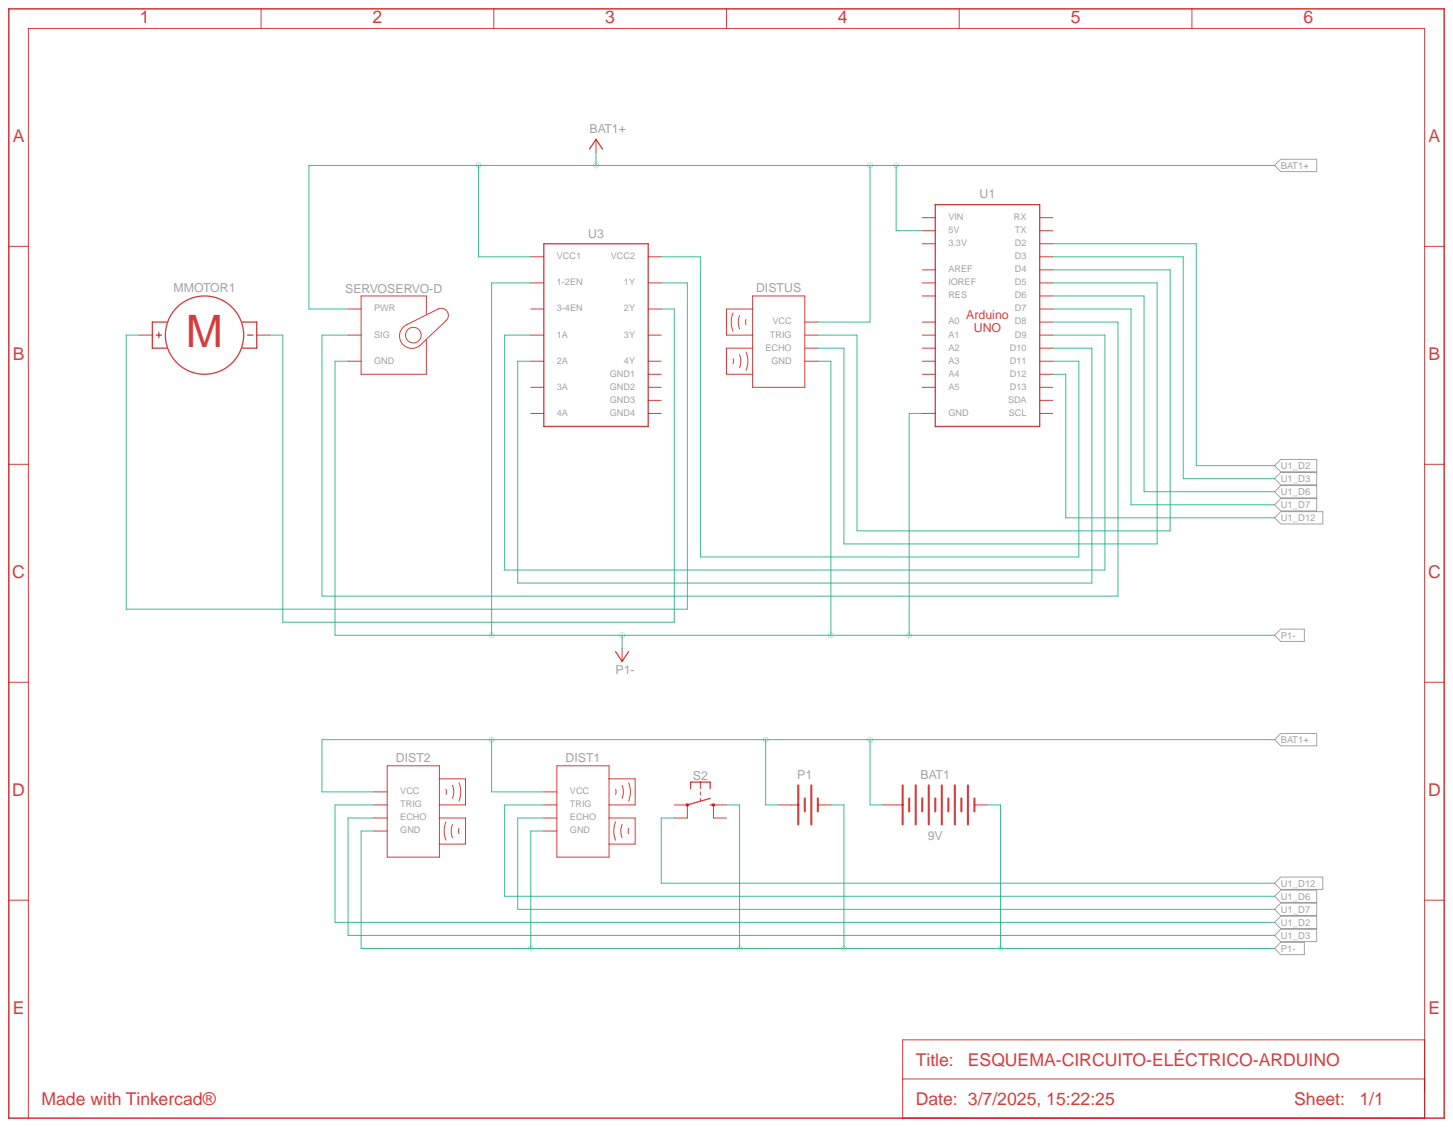
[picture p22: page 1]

Title: ESQUEMA-CIRCUITO-ELÉCTRICO-ARDUINO

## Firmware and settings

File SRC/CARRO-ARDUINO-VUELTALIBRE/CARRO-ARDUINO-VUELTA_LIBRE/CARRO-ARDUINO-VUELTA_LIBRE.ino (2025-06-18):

//CARRO-ARDUINO

  #include <Servo.h>
  #include <NewPing.h>
  Servo servo1Motor;
  Servo servo2Motor;

  // Definición de pines
  const int TRIGGER_PIN = 2;
  const int ECHO_PIN = 3;
  //TRACCION
  const int MOTOR_IN1 = 9;
  const int MOTOR_IN2 = 7;
  //DIRECCION
  const int SERV1 = 11;
  //ULTRASONIDO
  const int SERV2 = 12;

  // Configuración del sensor ultrasónico
  const int MAX_DISTANCE = 300; // Distancia máxima a medir en cm
  NewPing sonar(TRIGGER_PIN, ECHO_PIN, MAX_DISTANCE);

  // Configuración del servo
 // Servo direccion;

  // Variables globales
  int CRUCES_ESQUINA = 0;
  int CRUCES_NIVELACION = 0;
  int DISTANCIAINICIAL;
  const int DISTANCIA_MINIMA = 50; // Distancia mínima antes de girar (en cm)
  const int TIEMPO_ESPERA_INICIAL = 1000; // 3 segundos de espera inicial
  const int CRUCES_MAXIMOS = 12;
  int Arranque=0;

  void setup() {
    pinMode(4,INPUT_PULLUP);
    while(Arranque==0){
      if(digitalRead(4)==LOW){
        Arranque=1;
      }
    }
    
    // Configurar pines del motor
    pinMode(MOTOR_IN1, OUTPUT);
    pinMode(MOTOR_IN2, OUTPUT);
    // Configurar pines de la direccion
    servo1Motor.attach(SERV1);
    //Direccion ulson
    servo2Motor.attach(SERV2);

    // Esperar 3 segundos antes de arrancar
    delay(TIEMPO_ESPERA_INICIAL);
    Serial.begin(9600);
    Serial.println("Sensor Ultrasonico Hc-SR04");
    Serial.println("Write by Guille and Leo");
    DISTANCIAINICIAL = sonar.ping_cm();
  }

  void loop() {
    // Medir la distancia
    int DISTANCIA = sonar.ping_cm();
    if (CRUCES_ESQUINA >= CRUCES_MAXIMOS) {
      if(DISTANCIA<=DISTANCIAINICIAL){
       detenerCarro();
       return; // Terminar la ejecución
      }
    }else{
      // Mover el carro hacia adelante
      moverAdelante();
    }
    
    // Medir la distancia
    DISTANCIA = sonar.ping_cm();
    // Si detecta un obstáculo, girar a la izquierda
    if ((DISTANCIA > 0) && (DISTANCIA <= DISTANCIA_MINIMA)) {
      girarIzquierda();
      CRUCES_ESQUINA++;
      delay(1000); // Esperar un segundo después de girar
      centrarDireccion();
      delay(500);
      apuntarFullDerecha();
      
      if (DISTANCIA > 15){
        nivelarParedD();
        CRUCES_NIVELACION++;
        delay(250);
      }
        else {
          centrarDireccion();
      }

      if (DISTANCIA <10){
        nivelarParedI();
        CRUCES_NIVELACION++;
        delay(250);
      }
        else {
          centrarDireccion();
      }
      delay(500);
      apuntarFullCentro();
      centrarDireccion();
      delay(100);
      Serial.print("Distancia: ");
      Serial.println(DISTANCIA);
      Serial.print("Cruces: ");
      Serial.println(CRUCES_ESQUINA);
    
    }
  }

  void moverAdelante() {
    Serial.println("Adelante");
    digitalWrite(MOTOR_IN1, LOW);
    digitalWrite(MOTOR_IN2, HIGH);
  }

  void moverAtras() {
    Serial.println("Atras");
    digitalWrite(MOTOR_IN1, HIGH);
    digitalWrite(MOTOR_IN2, LOW);
  }

  void detenerCarro() {
    Serial.println("Detener");
    digitalWrite(MOTOR_IN1, LOW);
    digitalWrite(MOTOR_IN2, LOW);
  }

  void girarIzquierda() {
    Serial.println("Izquierda");
    servo1Motor.write(47);
  }
  void girarDerecha() {
    Serial.println("Derecha");
    servo1Motor.write(133);
  }

  void centrarDireccion() {
    Serial.println("Centrar");
    servo1Motor.write(90);
  }

  void apuntarFullDerecha() {
    Serial.println("FullDerecha");
    servo2Motor.write(1);
  }

  void apuntarFullIzquierda() {
    Serial.println("FullIzquierda");
    servo2Motor.write(135);
  }
  void apuntarFullCentro() {
    Serial.println("FullCentro");
    servo2Motor.write(90);
  }
  void nivelarParedD() {
    Serial.println("NivelandoD");
    servo1Motor.write(95);
  }
  void nivelarParedI() { 
    Serial.println("NivelandoI");
    servo1Motor.write(80);
  }

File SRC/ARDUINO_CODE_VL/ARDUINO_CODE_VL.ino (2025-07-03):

#include <Servo.h>
  #include <NewPing.h>
  Servo servo1Motor;

  // Definición de pines
  
  // ULTRASONIDOS 

  // DERECHO
  const int TRIGGER_DERECHA = 2;
  const int ECHO_DERECHA = 3;
  //CENTRAL
  const int TRIGGER_CENTRAL = 4;
  const int ECHO_CENTRAL = 5;
  //IZQUIERDO
  const int TRIGGER_IZQUIERDA = 6;
  const int ECHO_IZQUIERDA = 7;

  //TRACCION
  const int MOTOR_IN3 = 9;
  const int MOTOR_IN4 = 10;
  const int ENB = A0;
  int Arranque = 0;  //DIRECCION
  const int SERVO = 8;
  

  // CONFIGURACION DE SENSORES ULTRASONIDO
  const int MAX_DISTANCE = 300; // Distancia máxima a medir en cm
  NewPing sonarD(TRIGGER_DERECHA, ECHO_DERECHA, MAX_DISTANCE);
  NewPing sonarC(TRIGGER_CENTRAL, ECHO_CENTRAL, MAX_DISTANCE);
  NewPing sonarI(TRIGGER_IZQUIERDA, ECHO_IZQUIERDA, MAX_DISTANCE);

  // Variables globales
  int cruces = 0;
  const int DISTANCIA_CRUCE = 150; // Distancia mínima antes de girar (en cm)
  const int TIEMPO_ESPERA_INICIAL = 3000; // 3 segundos de espera inicial
  const int CRUCES_MAXIMOS = 12;

  // DISTANCIAS INICIALES
  int DISTANCIA_INICIAL_DERECHA = 0;
  int DISTANCIA_INICIAL_CENTRAL = 0;
  int DISTANCIA_INICIAL_IZQUIERDA = 0;

  // DISTANCIAS EN GENERAL
  int DISTANCIA_DERECHA = 0;
  int DISTANCIA_CENTRAL = 0;
  int DISTANCIA_IZQUIERDA = 0;

  void setup() {

    Serial.begin(9600);
    Serial.println("Ultrasonic Sensor Hc-SR04 Test");
    Serial.println("Write by Guille and Leo");

    // configurar pin del pulsador
    pinMode(11,INPUT_PULLUP);
    while(Arranque==0){
      if(digitalRead(11)==LOW){
        Arranque=1;
      }
    }


    // Configurar pines del motor
    pinMode(MOTOR_IN3, OUTPUT);
    pinMode(MOTOR_IN4, OUTPUT);
    // Configurar pines de la direccion
    servo1Motor.attach(SERVO);
   
    DISTANCIA_INICIAL_DERECHA = sonarD.ping_cm();
    DISTANCIA_INICIAL_CENTRAL = sonarC.ping_cm();
    DISTANCIA_INICIAL_IZQUIERDA = sonarI.ping_cm();

    // esperar 3 segundos antes de avanzar
     delay(TIEMPO_ESPERA_INICIAL);
     centrarDireccion();
     delay(500);
  }

  void loop() {

     // Medir la distancia
    DISTANCIA_DERECHA = sonarD.ping_cm();
    DISTANCIA_CENTRAL = sonarC.ping_cm();
    DISTANCIA_IZQUIERDA = sonarI.ping_cm();

    if (cruces >= CRUCES_MAXIMOS) {
      detenerCarro();
      return; // Terminar la ejecución
    }else{
      // Mover el carro hacia adelante
      moverAdelante();
    }

    // GIRAR DERECHA
    if ((DISTANCIA_DERECHA > 0) && (DISTANCIA_CENTRAL > 0) && (DISTANCIA_CENTRAL <= 100) && (DISTANCIA_DERECHA >= DISTANCIA_CRUCE)) {
      girarDerecha();
      cruces++;
      delay(1400); 
      centrarDireccion();
      delay(1000);
    }
    // GIRAR IZQUIERDA
    if ((DISTANCIA_IZQUIERDA > 0) && (DISTANCIA_CENTRAL > 0) && (DISTANCIA_CENTRAL <= 100) && (DISTANCIA_IZQUIERDA >= DISTANCIA_CRUCE)) {
      girarIzquierda();
      cruces++;
      delay(1400); 
      centrarDireccion();
      delay(1000);
    }
    // NIVELAR DERECHA
    if ((DISTANCIA_IZQUIERDA > 0) && (DISTANCIA_IZQUIERDA <= 15)){
    nivelarDerecha();
    delay(750);
    centrarDireccion();
    delay(200);
    }
    // NIVELAR IZQUIERDA
    if ((DISTANCIA_DERECHA > 0) && (DISTANCIA_DERECHA <= 15)){
    nivelarIzquierda();
    delay(750);
    centrarDireccion();
    delay(200);
    }

  }

  void moverAdelante() {
    Serial.println("Adelante");
    digitalWrite(MOTOR_IN3, LOW);
    digitalWrite(MOTOR_IN4, HIGH);
    analogWrite(ENB, 130); 
  }

  void moverAtras() {
    Serial.println("Atras");
    digitalWrite(MOTOR_IN3, HIGH);
    digitalWrite(MOTOR_IN4, LOW);
    analogWrite(ENB, 130); 
  }

  void detenerCarro() {
    Serial.println("Detener");
    digitalWrite(MOTOR_IN3, LOW);
    digitalWrite(MOTOR_IN4, LOW);
    analogWrite(ENB, 0); 
  }

  void girarIzquierda() {
    Serial.println("Izquierda");
    servo1Motor.write(50);
  }
  void girarDerecha() {
    Serial.println("Derecha");
    servo1Motor.write(144);
    
  }

  void centrarDireccion() {
    Serial.println("Centrar");
    servo1Motor.write(97);
    
  }
  void nivelarDerecha(){
    Serial.println("NivelarDerecha");
    servo1Motor.write(117);
    
  }
  void nivelarIzquierda(){
    Serial.println("NivelarIzuqierda");
    servo1Motor.write(77);
    
  }

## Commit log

2025-05-17 SUBIENDO DISEÑOS 3D
    [BARRA DIRECCIÓN.stl, BASE INFERIOR.stl, BASE SUPERIOR.stl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]
2025-06-07 ACTUALIZANDO DISEÑOS
    [SOPORTE RUEDAS TRACCION 2.stl]
2025-06-22 actualizando src y modelos
    [BARRA DIRECCIÓN.stl, BASE INFERIOR.stl, BASE SUPERIOR.stl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]
2025-06-24 SUBIENDO NUEVOS MODELOS
    [BARRA DIRECCION.stl, BARRA DIRECCIÓN.stl, BASE INFERIOR.stl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]
2025-06-30 AGREGANDO NUEVO MODELO GENERAL
    [SOPORTE RUEDAS DIRECCION.stl]
2025-06-30 agregando lista de componentes
2025-07-04 agregando esquema de la base superior
2025-07-04 Agregando ESP32-CAM
2025-07-04 agregando definicion de pines
